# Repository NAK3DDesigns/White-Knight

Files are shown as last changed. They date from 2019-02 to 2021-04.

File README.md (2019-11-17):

# White-Knight
White Knight Belt Printer
This repository contains all files necessary to build you own White Knight Belt printer..
Please bear with me as I continue to update files and process assembly videos

I believe all files have been converted to Fusion 360 now.  If you discover a file I've missed please open a new issue and I will get it converted and uploaded.. 

There are people trying to organize group buys for the belt materials..  see link below..
https://infinityprinters.org/t/group-buy-endless-belt/67

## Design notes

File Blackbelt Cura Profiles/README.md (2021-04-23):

# Blackbelt Cura Profiles

****this is still in testing****
Please leave feedback

To use this executable file you first need to install Blackbelt Cura 3.6.0 and the 3.6.0 Update 1...
https://blackbelt-3d.com/download-area/
Once installed just run this executable, it will install new profiles in Cura.
Once in Cura go to "Preferences", "Configure Cura", select "Printers" in the left window,
click "Add", select "NAK 3D Designs" 
Choose "Squire" or " White Knight"

****Update****

This should still work with the latest 3.6.2 version.

There are other options now available as well that support belt printing.

IdeaMaker - https://www.raise3d.com/download/

Kiri:moto - https://grid.space/kiri/

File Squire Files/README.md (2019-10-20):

# White-Knight
White Knight Belt Printer
This repository contains all files necessary to build you own White Knight Squire Belt printer..
I will continue to add files and BOM as I get them completed.  Currently all Fusion 360 files, STEP files, & the STL's for the main printer have been loaded..
I have also added the Assembly files..  They are not complete with all minor hardware but all major components are in place..

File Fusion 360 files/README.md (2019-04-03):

# White-Knight
White Knight Belt Printer
This repository contains Fusion 360 Files that have been test printed and verified to have correct dimensions and fit.

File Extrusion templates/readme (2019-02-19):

Files for aluminum extrusion templaes and aluminum tool plates

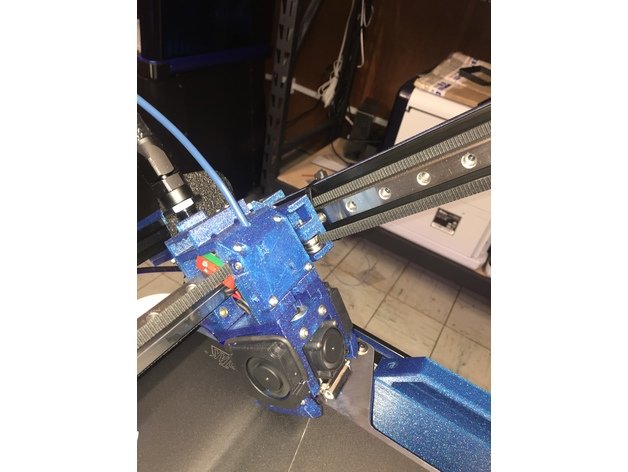
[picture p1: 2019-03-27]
Photos/White Knight 7.jpg

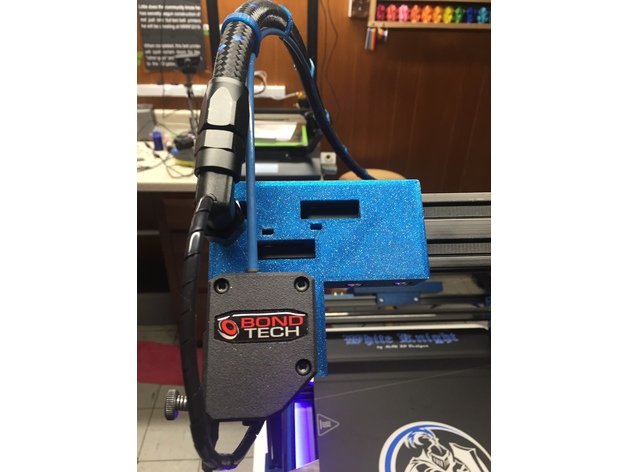
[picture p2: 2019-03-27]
Photos/White Knight 14.jpg

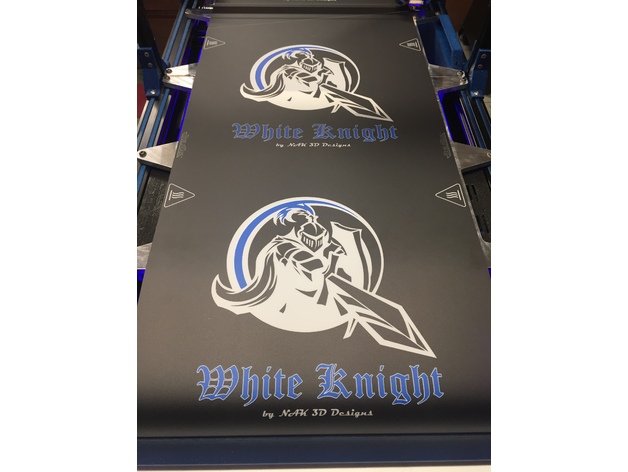
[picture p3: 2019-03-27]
Photos/White Knight 15.jpg

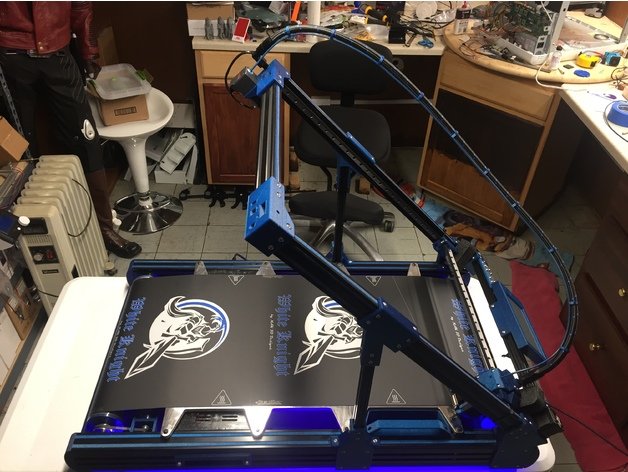
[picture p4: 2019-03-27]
Photos/White Knight 3.jpg

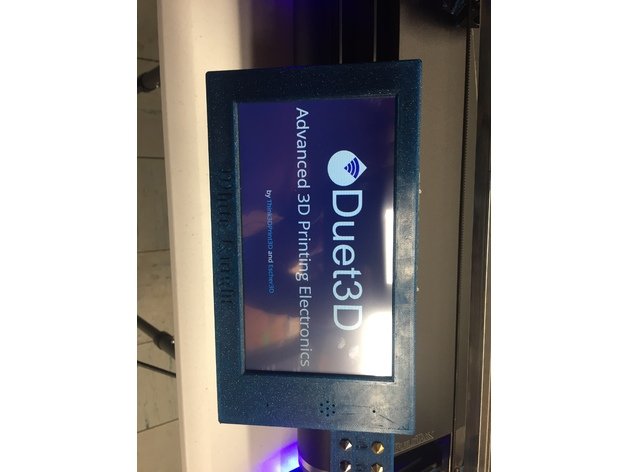
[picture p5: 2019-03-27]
Photos/White Knight 16.jpg

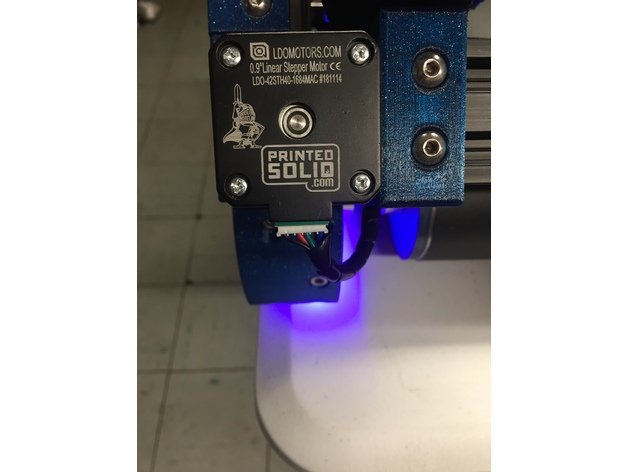
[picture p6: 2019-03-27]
Photos/White Knight 8.jpg

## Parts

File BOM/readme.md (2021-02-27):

# BOM
## Components
| Part | Qty | Cost | Source |
|---|-----|---|---|
| 100x Spring Loaded T-Nuts 2020 M4/M5 | 2 | $25.90  | Zyltec |
| MGN12 Linear Rail - 1000mm - One Carriage | 2 | $103.90 | Zyltec |
| MGN12 Linear Rail - 500mm - One Carriage | 1 | $34.95  | Zyltec |
| Extrusions | 1 | $154.39 | Openbuilds |
| Duet Wifi | 1 | $169.90 | Printed Solid |
| PanelDue 7i | 1 | $104.90 | Printed Solid |
| Bondtech BMG | 1 | $80.00  | Printed Solid |
| Mosquito Mount | 1 | $11.99  | Printed Solid |
| Mosquito Hotend | 1 | $144.80 | Printed Solid |
| Slice Thermistor | 1 | $39.99  | Printed Solid |
| Slice 50W heater | 1 | $18.80  | Printed Solid |
| LDO .9 Stepper | 3 | $45.00  | Printed Solid |
| Nema 17 5:1 geared stepper | 1 | $39.87  | E3D Online |
| F623zz Bearings | 20  | $12.00  | e-bay |
| 2GT Timing pulley 20Tooth 5mm Bore | 2 | $2.00 | e-bay |
| 2GT Timing pulley 20tooth 8mm Bore | 1 | $2.00 | e-bay |
| 60T 1/2 GT2 pulley | 1 | $13.00  | e-bay |
| 6202-2RS 1/2 ID bearing | 4 | $11.00  | thebigbearingstore.com |
| Micro switch endstop | 2 | $2.00 | Openbuilds |
| Aluminum tube 3"x16"x.125" (61ARDT3125) | 2 | $24.68  | Midweststeelsupply.com |
| Aluminum Tool Plate 3/8" x 15" x 20.5" (ALI38) | 1 | $50.64  | Midweststeelsupply.com |
| Aluminum tool plate 3/8" x 9" x 20.5" (ALI38) | 1 | $34.32  | Midweststeelsupply.com |
| 6061 Aluminum Square Bar 1/2" x 19" (61ASB12) | 1 | $7.95 | Midweststeelsupply.com |
| 303 Stainless Bearing Shaft(303SSBSQ12) 1/2 x 20.5"| 2 | $16.00  | Midweststeelsupply.com |
| Full hardened Stainless steel belt 400mm x 1920mm  | 1 | $265-$370 | Belttechnologies.com |
| **** Belt cost varies depending on Quantity ordered, group buys recommended  **** |
| Buildtak sheet 405mm x 2000mm (3 week lead time) | 1 | $290.00 | Buildtak.com |
| Meanwell LRS350-24 powersupply | 1 | $30.00  | Jameco.com #2219823 |
| Silicone Bed heater 200x400 24v(ebay item #143206149832)| 1 | $55.00  | e-bay |
| Rubber feet | 1 | $10.00  | e-bay |
| 1/2" x 19" aluminum sqaure bar | 1 | $7.95 | Midweststeelsupply.com |
| Noctua 40mm fans | 3 | $45.00  | Amazon |
| Roller drive belt A6R51M125060 | 1 | $6.00 | SDP/SI |
| 5 meters of GT2 Belt | 1 | $50.00  | SDP/SI |
| 24v Blower Fans | 2 | $18.00  | Tinymachines.com |
| stepper heat sink | 1 | $5.00 | Amazon part #A-0047 |
| Power Connector/switch | 1 | $3.00 | ebay item#152765834186 |
| Bulk Harware order (nuts, bolt, etc) | 1 | $202.73 | McMaster Carr |
| 3/8-in Push Connect x 1/4-in MIP Male Fitting | 1 | $3.78 | Lowes.com #835028 |
| 3/8-in Push Connect x 1/4-in MIP dia 90-Degree 	 | 1 | $4.18	 | Lowes.com #835045 |
| 3/8-in x 25-ft Polyethylene Tubing | 1 | $6.18 | Lowes.com #814305 |
|Buck converter (part # MP1584EN) | 1	 | $8.00	 | Amazon.com |

## Extrusions
| Size | Length | Qty |
|---|---|-----|
| 4080 C-Channel | 914mm  | 2 |
| 2040 V-slot | 520mm  | 3 |
| 2040 V-slot | 700mm  | 2 |
| 2040 V-slot | 460mm  | 1 |
| 2040 V-slot | 453mm  | 1 |
| 2020 V-slot | 315mm  | 2 |

## Bulk Hardware
| Item | Qty | Source | Part # | 
|---|-----|---|---|
| M2 x 12mm bolt | 8 | McMaster-Carr | 92095A455 | 
| M2 Nut | 2 | McMaster-Carr | 91828A111 | 
| M2 Heatset | 6 | McMaster-Carr | 94459A120 | 
| M3 Heatset | 48  | McMaster-Carr | 94180A331 | 
| M3 Washer | 18  | McMaster-Carr | 93475A210 | 
| M3 Star washer | 4 | McMaster-Carr | 95060A320 | 
| M3 Nut | 6 | McMaster-Carr | 91828A211 | 
| M3 x 8mm bolt | 46  | McMaster-Carr | 92095A181 | 
| M3 x 10mm bolt | 14  | McMaster-Carr | 92095A182 | 
| M3 x 12mm bolt | 10  | McMaster-Carr | 92095A183 | 
| M3 x 16mm bolt | 28  | McMaster-Carr | 92095A184 | 
| M3 x 18mm bolt | 2 | McMaster-Carr | 92095A472 | 
| M3 x 25mm bolt | 14  | McMaster-Carr | 92095A186 | 
| M3 x 30mm bolt | 1 | McMaster-Carr | 92095A187 | 
| M3 x 35mm bolt | 4 | McMaster-Carr | 92095A201 | 
| M3 x 45mm bolt | 2 | McMaster-Carr | 92095A474 | 
| M4 x 8mm bolt | 4 | McMaster-Carr | 92095A189 | 
| M5 Square nut | 4 | McMaster-Carr | 90225A101 | 
| M5 T-nuts | 118 | Zyltec.com | HW-M5-SPRNG-T-NUT-100PK | 
| M5 high temp washers | 10  | McMaster-Carr | 93785A214 | 
| M5 x 15mm high temp/nylon washer| 10  | | | 
| M5 x 8mm Button Bolt | 104 | McMaster-Carr | 92095A207 | 
| M5 x 16mm Bolt | 23  | McMaster-Carr | 91292A126 | 
| M5 x 18mm Button Bolt | 10  | McMaster-Carr | 92095A481 | 
| M5 x 30mm Bolt | 18  | McMaster-Carr | 91292A192 | 
| #2 x3/8in thread cutting screws | 2 | | | 
| JST connectors | 6 | ebay | | 
| Shaft Collar | 7 | McMaster-Carr | 9946K15 | 
| M3 x8mm Knurled screw | 2 | McMaster-Carr | 92545A111 | 

## Wire Harness
| Item | Qty | Source | Part # | 
|---|-----|---|---|
| 34 Pin Male IDC connector | 1 | TME.com | AWHP-34P | 
| 34 Pin Female IDC Connector | 1 | Digikey.com | 3M157228-ND | 
| 4 position Molex Plug | 1 | Digikey.com | WM1018-ND | 
| 4 position Molex receptical | 1 | Digikey.com | WM3701-ND | 
| Molex Male pin | 4 | Digikey.com | WM2500-ND | 
| Molex female pin | 4 | Digikey.com | WM2501-ND | 
| 20AWG 2 conductor blk/red | 1 | Digikey.com | CN180BR-25-ND | 
| 26AWG 34 cond multi color ribbon| 1 | Digikey.com | 3M157870-25-ND | 

## 34 pin connector pinout
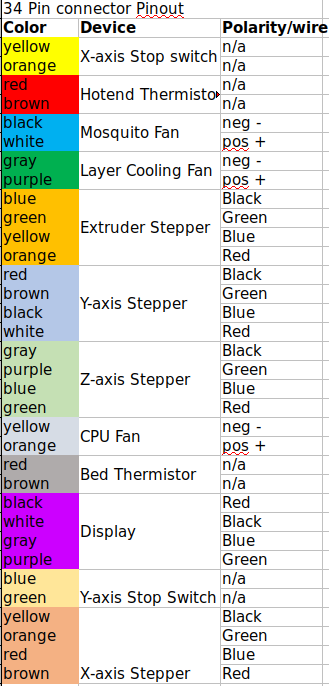
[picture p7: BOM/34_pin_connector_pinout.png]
pinout


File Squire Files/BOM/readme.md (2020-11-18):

# BOM
## Components
| Part | Qty | Cost | Source |
|---|-----|---|---|
| 100x Spring Loaded T-Nuts 2020 M4/M5 | 2 | $25.90  | Zyltec |
| LDO MGN12H Linear Rail - 400mm - Single Carriage | 3 | $120.00 | Printed Solid |
| Extrusions | 1 | $115.00 | Openbuilds |
| Duet Wifi | 1 | $169.90 | Printed Solid |
| Duet Filament Monitor Rotating Magnet Version | 1 | $52.95  | Printed Solid |
| PanelDue 5i | 1 | $89.90  | Printed Solid |
| Bondtech BMG | 1 | $80.00  | Printed Solid |
| E3Dv6 hotend & nozzle (hand filed edge) | 1 | $85.00  | Printed Solid |
| LDO .9 Stepper LDO-42STH40-1684MAC | 2 | $32.00  | Printed Solid |
| LDO .9 slim stepper LDO-42STH25-1404MAC | 1 | $15.00  | Printed Solid |
| LDO 5:1 geared stepper | 1 | $39.87  | Printed Solid |
| LDO 2GT 16T Idler with 3mm Bore | 8 | $48.00  | Printed Solid |
| Balitensen Toothless GT2 Idler Pulley 16T 3mm Bore | 2 | $7.90 | Amazon |
| 2GT Timing pulley 20Tooth 5mm Bore | 2 | $2.00 | e-bay |
| 2GT Timing pulley 20tooth 8mm Bore | 1 | $2.00 | e-bay |
| 6202-2RS 1/2 ID bearing | 3 | $9.00 | thebigbearingstore.com |
| Micro switch endstop | 2 | $2.00 | Openbuilds |
| Aluminum tube 3" x 9.5"x.125" (61ARDT3125) | 2 | $16.77  | Midweststeelsupply.com |
| Aluminum Tool Plate 1/4" x 4" x 15.75" (ALI38) | 1 | $16.39  | Midweststeelsupply.com |
| Aluminum tool plate 1/4" x 6" x 15.75" (ALI38) | 1 | $24.82  | Midweststeelsupply.com |
| 6061 Aluminum Square Bar 1/2" x 14.25" (61ASB12) | 1 | $7.95 | Midweststeelsupply.com |
| 303 Stainless Bearing Shaft 1/2" x 15.75"(303SSBSQ12)| 2 | $14.00  | Midweststeelsupply.com |
| Full hardened Stainless steel belt 240mm x 1085mm  | 1 | $265-370 | Belttechnologies.com  |
| **** Belt cost varies depending on Quantity ordered, group buys recommended  **** |
| Buildtak sheet 250mm x 1185mm (3 week lead time) | 1 | $175.00 | Buildtak.com |
| Meanwell LRS350-24 powersupply | 1 | $30.00  | Jameco.com #2219823 |
| Silicone Bed heater (ebay item #143351332434) | 1 | $34.00  | e-bay |
| SUNON 40mm fans | 5 | $52.00  | Printed Solid |
| Buck converter (part # MP1584EN)				 	 | 1 | $8.00 | Amazon.com |
| 8mm to 12mm shaft coupler | 1 | $10.25  | E-bay |
| 4 meters of GT2 Belt | 1 | $40.00  | Printed Solid |
| BerdAir  Max 24V with eswitch kit | 1 | $48.50  | themakerhive.com |
| stepper heat sink | 1 | $5.00 | Amazon part #A-0047 |
| Power Connector/switch | 1 | $3.00 | ebay item#152765834186 |
| Bulk Harware order (nuts, bolt, etc) | 1 | $202.73 | McMaster Carr |
| 3/8-in Push Connect x 1/4-in NPT Male Fitting | 2 | $15.06  | McMaster-Carr #5523K19 |
| 3/8-in x 25-ft Polyethylene Tubing | 1 | $6.18 | Lowes.com #814305 |

## Extrusions
| Size | Length | Qty |
|---|---|-----|
| 4080 C-Channel | 500mm  | 2 |
| 2040 V-slot | 400mm  | 4 |
| 2040 V-slot | 336mm  | 1 |
| 2040 V-slot | 370mm  | 1 |
| 2040 V-slot | 160mm  | 2 |
| 2040 V-slot | 387mm  | 2 |
| 2020 V-slot | 190mm  | 2 |

## Bulk Hardware
| Item | Qty | Source | Part # | 
|---|-----|---|---|
| M2.5 x 12mm bolt | 2 | McMaster-Carr | 92095A461 | 
| M2.5 Nut | 2 | McMaster-Carr | 91828A113 |
| M3 Heatset | 55  | McMaster-Carr | 94180A331 | 
| M3 Washer | 4 | McMaster-Carr | 93475A210 | 
| M3 Nut | 6 | McMaster-Carr | 91828A211 | 
| M3 x 8mm bolt | 60  | McMaster-Carr | 92095A181 | 
| M3 x 10mm bolt | 14  | McMaster-Carr | 92095A182 | 
| M3 x 12mm bolt | 10  | McMaster-Carr | 92095A183 | 
| M3 x 16mm bolt | 28  | McMaster-Carr | 92095A184 | 
| M3 x 18mm bolt | 2 | McMaster-Carr | 92095A472 | 
| M3 x 25mm bolt | 14  | McMaster-Carr | 92095A186 | 
| M3 x 30mm bolt | 1 | McMaster-Carr | 92095A187 | 
| M3 x 35mm bolt | 4 | McMaster-Carr | 92095A201 |
| M3 x 40mm bolt | 3 | McMaster-Carr | 92095A203 |
| M3 x 45mm bolt | 2 | McMaster-Carr | 92095A474 | 
| M4 x 8mm bolt | 8 | McMaster-Carr | 92095A189 | 
| M5 Square nut | 4 | McMaster-Carr | 90225A101 | 
| M5 T-nuts | 164 | Zyltec.com | HW-M5-SPRNG-T-NUT-100PK | 
| M5 high temp washers | 8 | McMaster-Carr | 93785A214 | 
| M5 x 15mm high temp/nylon washer| 8 | | | 
| M5 x 8mm Button Bolt | 156 | McMaster-Carr | 92095A207 | 
| M5 x 16mm Bolt | 21  | McMaster-Carr | 91292A126 | 
| M5 x 18mm Button Bolt | 8 | McMaster-Carr | 92095A481 | 
| M5 x 30mm Bolt | 12  | McMaster-Carr | 91292A192 | 
| #2 x3/8in thread cutting screws | 2 | | | 
| JST connectors | 6 | ebay | | 
| Shaft Collar | 6 | McMaster-Carr | 9946K15 |
| Stacked wave spring 5mm shaft | 4 | McMaster-Carr | 1561T732 | 

## Wire Harness
| Item | Qty | Source | Part # | 
|---|-----|---|---|
| 40 Pin Male IDC connector | 1 | Digikey.com | OR973-ND | 
| 40 Pin Female IDC Connector | 1 | Digikey.com | OR923-ND | 
| 4 position Molex Plug | 2 | Digikey.com | WM1018-ND | 
| 4 position Molex receptical | 2 | Digikey.com | WM3701-ND | 
| Molex Male pin | 4 | Digikey.com | WM2500-ND | 
| Molex female pin | 4 | Digikey.com | WM2501-ND | 
| 20AWG 2 conductor blk/red | 1 | Digikey.com | CN180BR-25-ND | 
| 26AWG 40 cond multi color ribbon| 1 | Digikey.com | 3M157900-25-ND | 

## Hotend Quick disconnect Bread Board
| Item | QTY | Source | Part # |
|---|-----|---|---|
| Molex MicroFit 3.0 6 Pos Header | 1 | Digikey.com | WM4037-ND |
| Molex Microfit 3.0 2 Pos header | 3 | Digikey.com | WM1922-ND |
| Molex Microfit 3.0 6 Pos Recpt  | 1 | Digikey.com | WM1785-ND |
| Molex Microfit 3.0 conn socket  | 25  | Digikey.com | WM1125CT-ND |
| Adafruit Jumper wire 22awg | 1 | Digikey.com | 1528-1743-ND |
| Gikfun Breadboard GK1009 | 1 | Amazon.com | GK1009 |

## 40 pin connector pinout
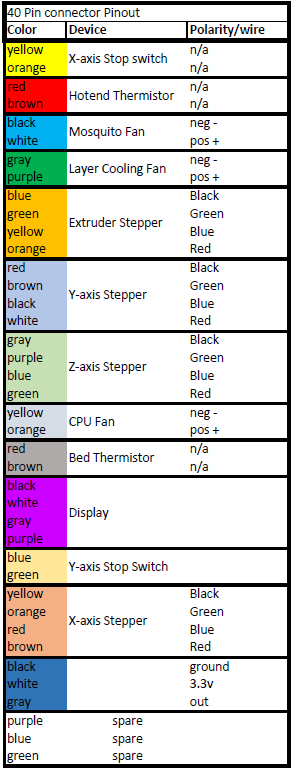
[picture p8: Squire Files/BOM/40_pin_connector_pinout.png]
pinout


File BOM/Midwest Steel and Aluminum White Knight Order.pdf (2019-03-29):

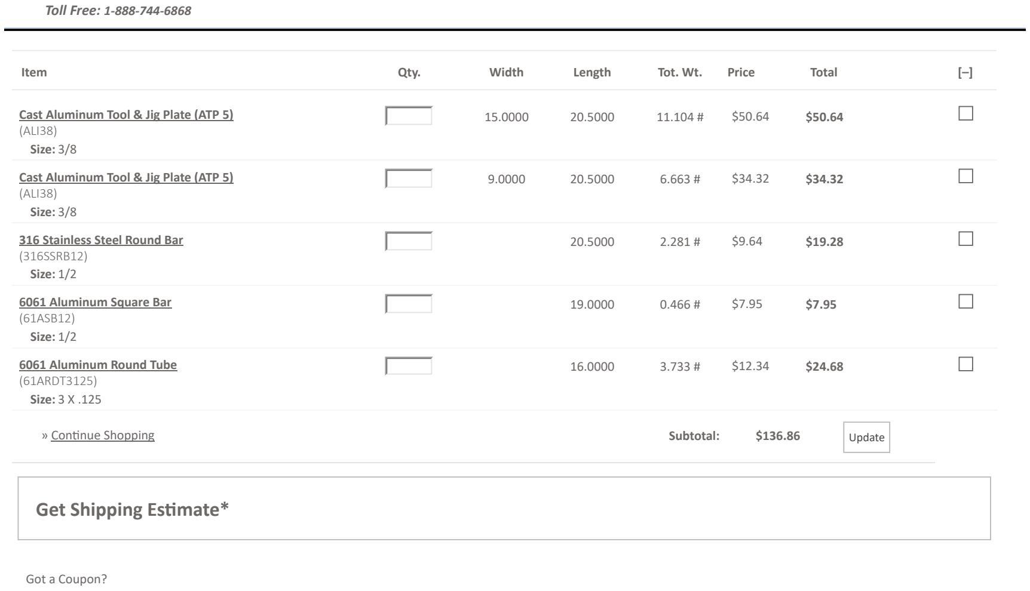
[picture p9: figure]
Toll Free: 1-888-744-6868; Cast Aluminum Tool & Jig Plate (ATP 5) (ALI38) Size: 3/8; 316 Stainless Steel Round Bar (316SSRB12) Size: 1/2; 6061 Aluminum Square Bar (61ASB12) Size: 1/2; 6061 Aluminum Round Tube (61ARDT3125) Size: 3 X .125; Item; Qty.; Width; Length; Tot. Wt.; Price; Total; » Continue Shopping; Subtotal:; Update; Get Shipping Estimate*; Got a Coupon?

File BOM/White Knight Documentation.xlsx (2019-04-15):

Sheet: 34pin connector
34 Pin connector Pinout
Color | Device | Polarity/wire
yellow | X-axis Stop switch | n/a
orange |  | n/a
red | Hotend Thermistor | n/a
brown |  | n/a
black | Mosquito Fan | neg -
white |  | pos +
gray | Layer Cooling Fan | neg -
purple |  | pos +
blue | Extruder Stepper | Black
green |  | Green
yellow |  | Blue
orange |  | Red
red | Y-axis Stepper | Black
brown |  | Green
black |  | Blue
white |  | Red
gray | Z-axis Stepper | Black
purple |  | Green
blue |  | Blue
green |  | Red
yellow | CPU Fan | neg -
orange |  | pos +
red | Bed Thermistor | n/a
brown |  | n/a
black | Display | Red
white |  | Black
gray |  | Blue
purple |  | Green
blue | Y-axis Stop Switch | n/a
green |  | n/a
yellow | X-axis Stepper | Black
orange |  | Green
red |  | Blue
brown |  | Red

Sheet: BOM
BOM |  |  |  | Total | $2042.92
Part | Cost | source
Linear Rails | $175.00 | Zyltec
Extrusions | $154.39 | Openbuilds
Duet Wifi | $169.90 | Printed Solid
PanelDue 7i | $104.90 | Printed Solid
Bondtech BMG | $80.00 | Printed Solid
Mosquito Mount | $11.99 | Printed Solid
Mosquito Hotend | $144.80 | Printed Solid
Slice Thermistor | $39.99 | Printed Solid
Slice 50W heater | $18.80 | Printed Solid
LDO .9 Stepper 1 | $15.00 | Printed Solid
LDO .9 Stepper 2 | $15.00 | Printed Solid
LDO .9 Stepper 3 | $15.00 | Printed Solid
Nema 17 5:1 geared stepper | $39.87 | E3D Online
623zz Bearings QTY 20 | $12.00 | e-bay
2GT Timing Pulley 20 Tooth 5mm bore | $2.00 | e-bay
2GT Timing Pulley 20 Tooth 8mm bore | $2.00 | e-bay
60T 1/2 GT2 pulley | $13.00 | e-bay
6202RS2 1/2 ID bearing QTY 4 | $11.00 | thebigbearingstore.com
Micro switch endstop Qty 2 | $2.00 | Openbuilds
Aluminum tube 3"x16"x.125" qty 2 | $24.68 | Midweststeelsupply.com
Aluminum Tool Plate 3/8" x 15" x 20.5" | $50.64 | Midweststeelsupply.com
Aluminum tool plate 3/8" x 9" x 20.5" | $34.32 | Midweststeelsupply.com
Stainless Steel Round Bar 1/2" x 20.5" | $19.28 | Midweststeelsupply.com
Full hardened Stainless steel belt 400mm x 1920mm | $210.00 | Belttechnologies.com
Buildtak sheet | $290.00 | Buildtak
Zyltec 2020 T-nuts Qty 200 | $30.00 | Zyltec
Meanwell LRS350-24 powersupply | $30.00 | jameco.com #2219823
Silicone Bed heater | $55.00 | e-bay
Rubber feet | $10.00 | e-bay
1/2" x 19" aluminum sqaure bar | $7.95 | Midweststeelsupply.com
Noctua 40mm fans Qty 3 | $45.00 | Amazon
3/8 PTFE, and fittings | $12.00 | Lowes
Roller drive belt A6R51M125060 | $6.00 | SDP/SI
5 meters of GT2 Belt | $50.00 | SDP/SI
24v Blower Fans QTY 2 | $18.00 | Tinymachines.com
stepper heat sink | $5.00 | ebay
Bulk Harware order (nuts, bolt, etc) | $202.73 | McMaster Carr | Broke down in Bulk hardware tab
34 Pin Male IDC connector | $1.32 | TME.com | AWHP-34P
34 Pin Female IDC Connector | $1.38 | Digikey.com | 3M157228-ND
4 position Molex Plug | $0.36 | Digikey.com | WM1018-ND
4 position Molex receptical | $0.31 | Digikey.com | WM3701-ND
Molex Male pin | $1.68 | Digikey.com | WM2500-ND
Molex female pin | $1.70 | Digikey.com | WM2501-ND
20AWG 2 conductor blk/red | $19.54 | Digikey.com | CN180BR-25-ND
26AWG 34 cond multi color ribbon | $50.25 | Digikey.com | 3M157870-25-ND
3/8-in Push Connect x 1/4-in MIP Male Fitting | $3.78 | Lowes.com #835028
3/8-in Push Connect x 1/4-in MIP dia 90-Degree | $4.18 | lowes.com #835045
3/8-in x 25-ft Polyethylene Tubing | $6.18 | lowes.com #814305

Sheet: Infill percentges
File | Infill | Nozzle | Perimeters | Layer Height
1-All_Belt_Clamps V2.stl | 85% | 0.4 | 4 | 0.2
1-Belt stepper mount Pt1 V4.stl | 50% | 0.4 | 4 | 0.2
1-Belt_stepper_mount_Pt2_V3.stl | 50% | 0.4 | 4 | 0.2
1-CBA bottom Cover V3 - part 1of3.stl | 5% | 0.8 | 2 | 0.2
1-CBA bottom Cover V3 - part 2of3.stl | 5% | 0.8 | 2 | 0.2
1-CBA bottom Cover V3 - part 3of3.stl | 5% | 0.8 | 2 | 0.2
1-CBA bottom Cover V3 Full.stl | 5% | 0.8 | 2 | 0.2
1-CBA top Cover V5 part 1of3.stl | 5% | 0.8 | 2 | 0.2
1-CBA top Cover V5 part 2of3.stl | 5% | 0.8 | 2 | 0.2
1-CBA top Cover V5 part 3of3.stl | 5% | 0.8 | 2 | 0.2
1-CBA top Cover V5.stl | 5% | 0.8 | 2 | 0.2
1-CBA_slide_tray_assembly_v11.stl | 25% | 0.4 | 4 | 0.2
1-Cooling fan Ducts v4.stl | 50% | 0.4 | 4 | 0.2
1-Display_Support_Endcaps.stl | 25% | 0.4 | 4 | 0.2
1-Mosquito & E3Dv6 Mount V7.stl | 50% | 0.4 | 4 | 0.2
1-Mosquito & E3Dv6 clamp and cooling fan mount V4.stl | 50% | 0.4 | 4 | 0.2
1-PanelDue7i_mount.stl | 50% | 0.4 | 4 | 0.2
1-PanelDue_7i_Version_2_Back.stl | 50% | 0.4 | 4 | 0.2
1-PanelDue_7i_Version_2_Front WK.stl | 50% | 0.4 | 4 | 0.2
1-Peeler.stl | 0% | 0.8 | 2 | 0.4
1-Rear_Idler_Right_V5.stl | 50% | 0.4 | 4 | 0.2
1-Rear_Idler_left_V4.stl | 50% | 0.4 | 4 | 0.2
1-Side_Support_Top_Brace_Left_V2.stl | 50% | 0.4 | 4 | 0.2
1-Side_Support_Top_Brace_Right_V2.stl | 50% | 0.4 | 4 | 0.2
1-Stepper_Mount_Left_V9.stl | 50% | 0.4 | 4 | 0.2
1-Stepper_Mount_Right_V9.stl | 50% | 0.4 | 4 | 0.2
1-Xaxis_Mount_Left_V11.stl | 50% | 0.4 | 4 | 0.2
1-Xaxis_Mount_Right_V10.stl | 50% | 0.4 | 4 | 0.2
1-hotend wire cover V3.stl | 50% | 0.4 | 4 | 0.2
1-hotend_carriage_v6.stl | 50% | 0.4 | 4 | 0.2
1-plug mount.stl | 50% | 0.4 | 4 | 0.2
1-slide tray end cover v4.stl | 50% | 0.4 | 4 | 0.2
1-tensioner mount bracket.stl | 50% | 0.4 | 4 | 0.2
10-Bowden_Cable_Clip_V1.stl | 85% | 0.4 | 4 | 0.2
2-4080 c-beam endcap V5.stl | 50% | 0.4 | 4 | 0.1
2-4080 c-beam endcap wider v1.stl | 50% | 0.4 | 4 | 0.1
2-Roller_Insert.stl | 25% | 0.4 | 4 | 0.2
2-Side_Support_Bottom_Brace.stl | 50% | 0.4 | 4 | 0.2
3-Pulley_Bearing_Mount_V2.stl | 50% | 0.4 | 4 | 0.2
4-Roller_End_Cap.stl | 25% | 0.4 | 4 | 0.2
switch enclosure V4.stl | 85% | 0.4 | 4 | 0.2
Drip Tray V2.stl | 50% | 0.4 | 4 | 0.2
Drip Tray handle.stl | 50% | 0.4 | 4 | 0.2

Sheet: Extrusions
Extrusions
Size | Length | Quantity
4080 C-Channel | 914mm | 2
2040 V-slot | 520mm | 3
2040 V-slot | 700mm | 2
2040 V-slot | 460mm | 1
2040 V-slot | 453mm | 1
2020 V-slot | 315mm | 2

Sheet: Bulk Hardware
Item | Qty | source | part#
M2 x 12mm bolt | 8 | McMaster-Carr | 92095A455
M2 Nut | 2 | McMaster-Carr | 91828A111
M2 Heatset | 6 | McMaster-Carr | 94459A120
M3 Heatset | 48 | McMaster-Carr | 94180A331
M3 Washer | 18 | McMaster-Carr | 93475A210
M3 Star washer | 4 | McMaster-Carr | 95060A320
M3 Nut | 6 | McMaster-Carr | 91828A211
M3 x 8mm bolt | 46 | McMaster-Carr | 92095A181
M3 x 10mm bolt | 14 | McMaster-Carr | 92095A182
M3 x 12mm bolt | 10 | McMaster-Carr | 92095A183
M3 x 16mm bolt | 28 | McMaster-Carr | 92095A184
M3 x 18mm bolt | 2 | McMaster-Carr | 92095A472
M3 x 25mm bolt | 14 | McMaster-Carr | 92095A186
M3 x 30mm bolt | 1 | McMaster-Carr | 92095A187
M3 x 35mm bolt | 4 | McMaster-Carr | 92095A201
M3 x 45mm bolt | 2 | McMaster-Carr | 92095A474
M4 x 8mm bolt | 4 | McMaster-Carr | 92095A189
M5 Square nut | 4 | McMaster-Carr | 90225A101
M5 T-nuts | 118 | Zyltec.com | HW-M5-SPRNG-T-NUT-100PK
M5 high temp washers | 10 | McMaster-Carr | 93785A214
M5 x 15mm custom washer | 10
M5 x 8mm Button Bolt | 104 | McMaster-Carr | 92095A207
M5 x 16mm Bolt | 23 | McMaster-Carr | 91292A126
M5 x 18mm Button Bolt | 10 | McMaster-Carr | 92095A481
M5 x 30mm Bolt | 18 | McMaster-Carr | 91292A192
#2 x3/8in thread cutting screws | 2
JST connectors | 6
Shaft Collar | 7 | McMaster-Carr | 9946K15
M3 x8mm Knurled screw | 2 | McMaster-Carr | 92545A111

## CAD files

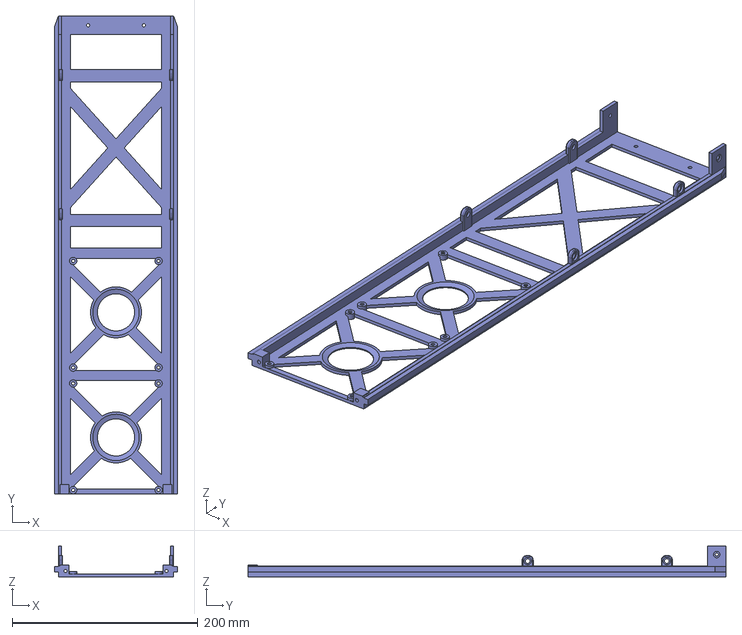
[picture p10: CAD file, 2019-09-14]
Fusion 360 files/1-CBA_slide_tray_assembly_v11 v2.step
133.1 x 515.2 x 33.0 mm

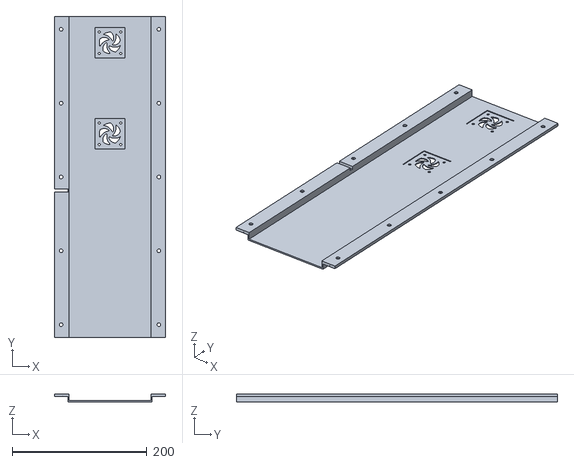
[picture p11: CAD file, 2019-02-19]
Printer STL's/1-CBA bottom Cover V3 Full.stl
165.0 x 476.0 x 12.0

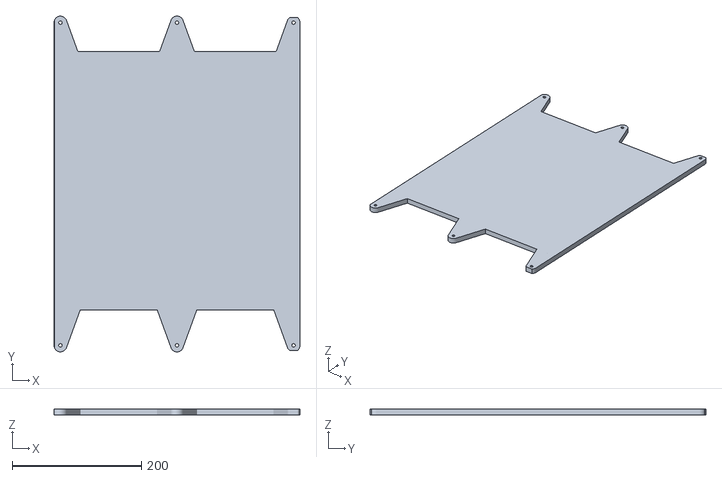
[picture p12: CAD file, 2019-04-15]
Extrusion templates/1x-Cold Build Plate V3.stl
381.0 x 520.0 x 9.52

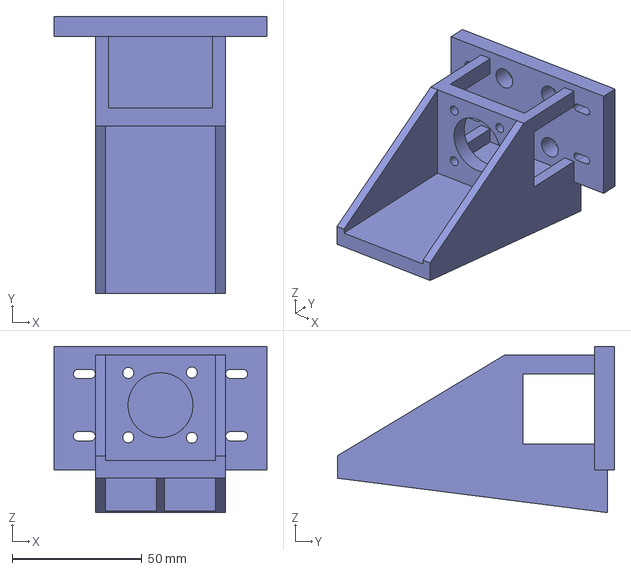
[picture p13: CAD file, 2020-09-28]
Fusion 360 files/1-Belt stepper mount Pt1 - LDO-42STH40-1204ACPG5 - V1.step
82.0 x 106.8 x 64.0 mm

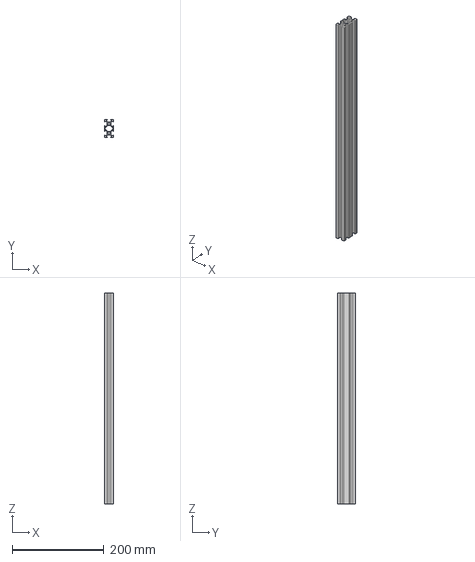
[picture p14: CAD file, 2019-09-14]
Fusion 360 files/Extrusion templates/1x 460mm 2040 v1.step
20.0 x 40.0 x 460.0 mm

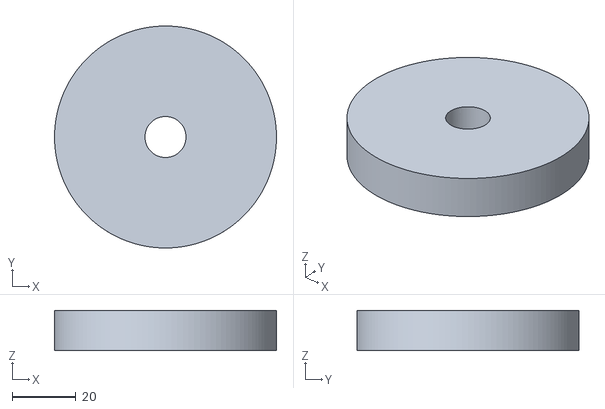
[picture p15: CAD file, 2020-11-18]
Printer STL's/2-Roller_Insert.stl
69.8 x 69.8 x 12.7

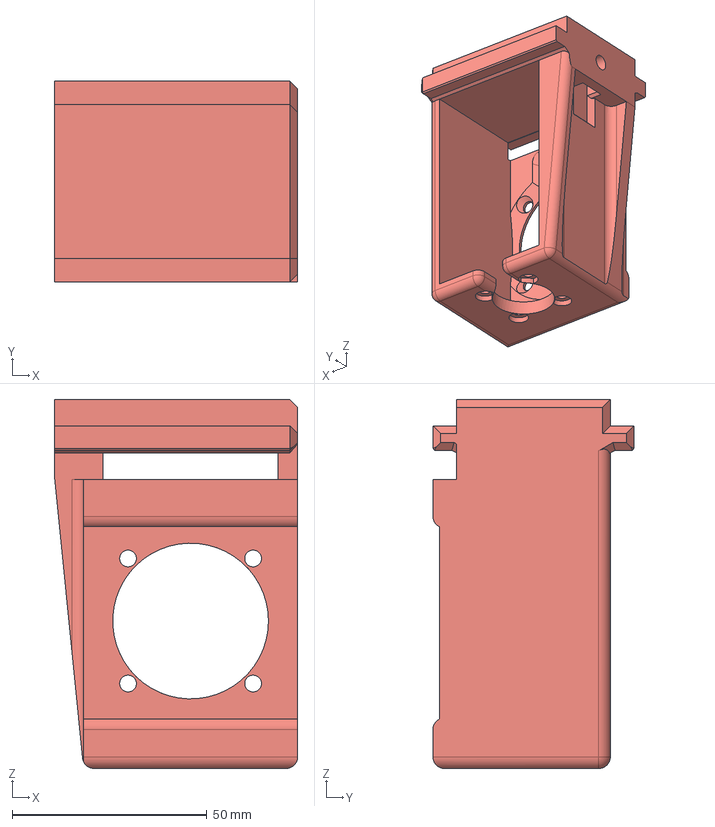
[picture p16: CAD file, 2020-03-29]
Squire Files/STEP Files/1-Belt Stepper direct drive Mount2 for E3D v2.step
62.5 x 51.7 x 94.8 mm

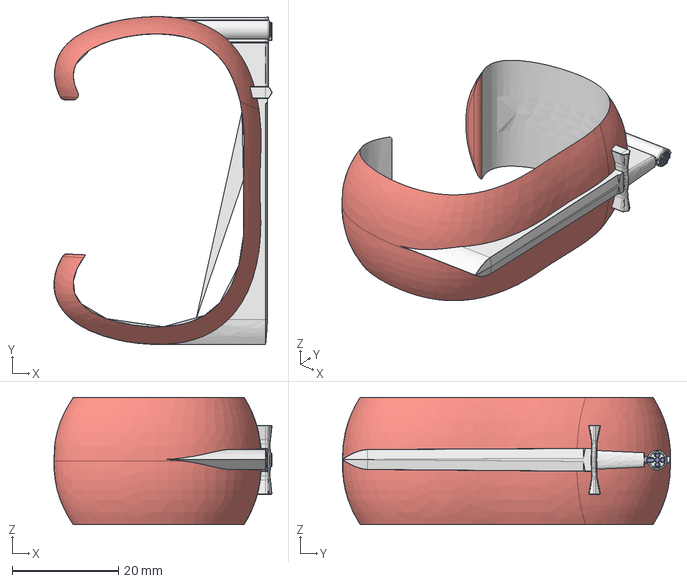
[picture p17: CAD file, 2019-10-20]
Squire Files/STEP Files/Scales/2040 extrusion top cover part 3.step
41.1 x 61.8 x 24.0 mm

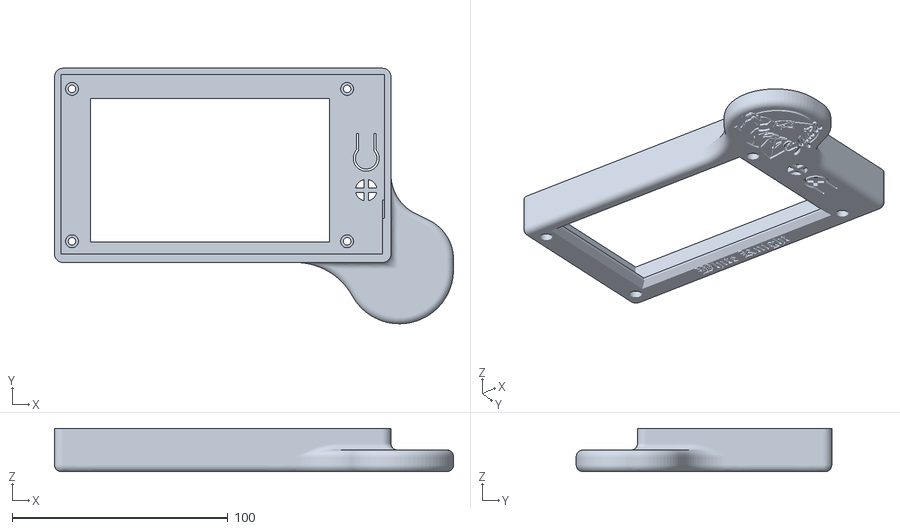
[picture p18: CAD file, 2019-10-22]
Squire Files/STL Files/1-5i_Case_Front Knight v14.stl
184.9 x 118.4 x 20.0

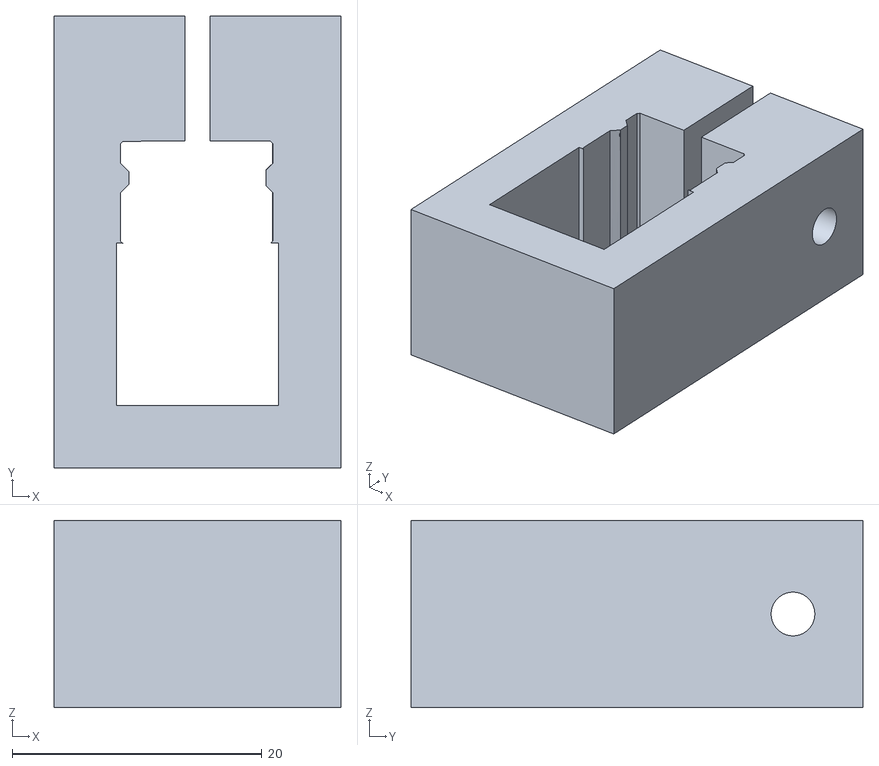
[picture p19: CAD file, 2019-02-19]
Tools STL's/linear rail alignment tool 2.stl
23.0 x 36.2 x 15.0

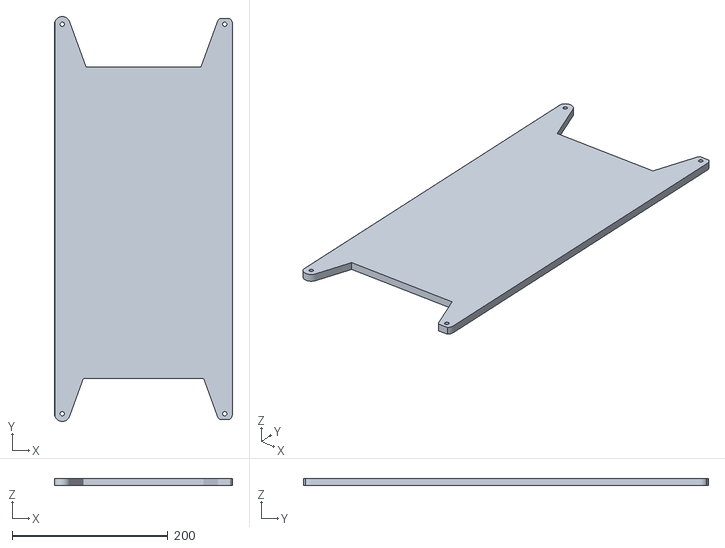
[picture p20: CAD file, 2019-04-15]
Extrusion templates/1x-Heated Build Plate V3.stl
228.6 x 520.0 x 9.53

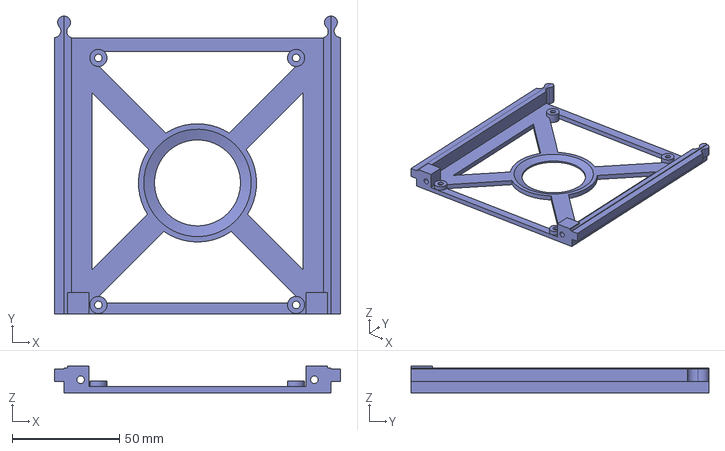
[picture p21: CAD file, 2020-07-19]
Fusion 360 files/CBA _Slide_Tray_Part_1of4 v2.step
133.1 x 138.7 x 12.5 mm

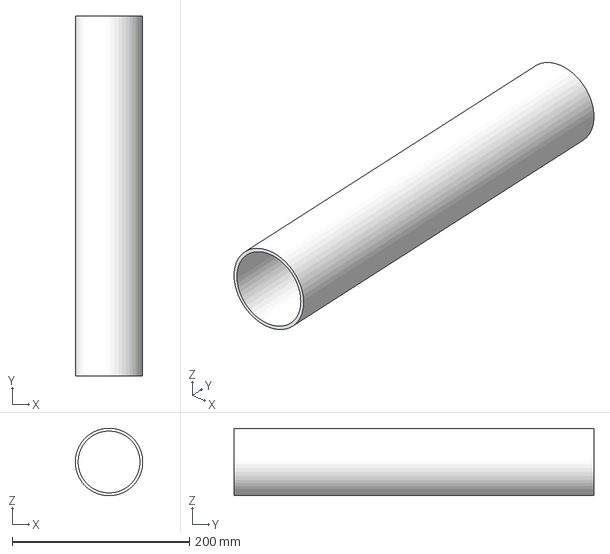
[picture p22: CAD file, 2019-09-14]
Fusion 360 files/Extrusion templates/2-3 inch aluminum roller tube v3.step
76.1 x 406.4 x 76.2 mm

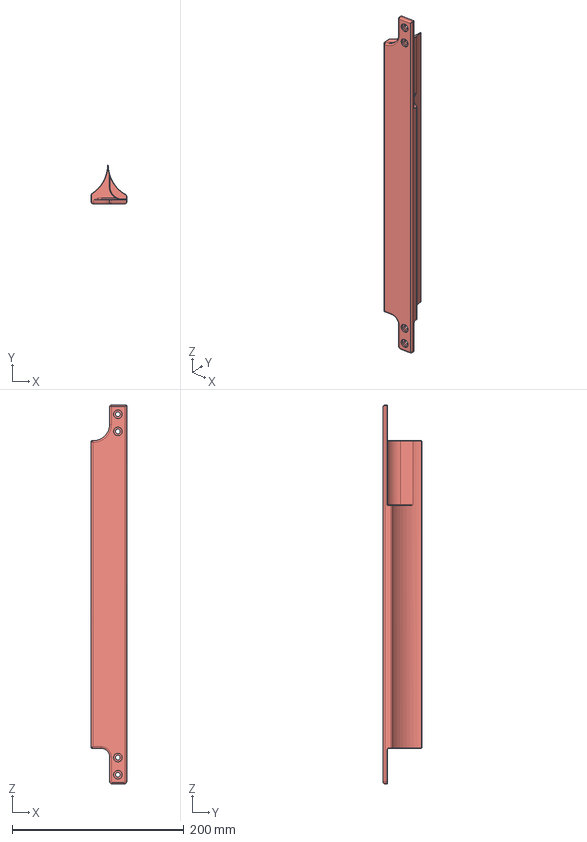
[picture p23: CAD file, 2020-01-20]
Squire Files/STEP Files/1-Peeler V4 v2.step
41.4 x 45.0 x 441.0 mm

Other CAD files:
Fusion 360 files/1-CBA_bottom_Cover_V3_Full v2.step
Printer STL's/1-Belt stepper mount Pt1 - LDO-42STH40-1204ACPG5 - V1.stl
Squire Files/STL Files/1-Squire CBA Top Cover 2 v2 part 1.stl
Tools STL's/roller jig.stl
Extrusion templates/1x-Cold Build Plate.stl
Extrusion templates/1x-Heated Build Plate.stl
Extrusion templates/1x_453mm_2040.stl
Extrusion templates/1x_460mm_2040.stl
Extrusion templates/2x_315mm_2020.stl
Extrusion templates/2x_700mm_2040.stl
Extrusion templates/3x_520mm_2040.stl
Fusion 360 files/1-Belt stepper mount Pt1 - LDO-42STH40-1204ACPG5 - V1.f3d
Fusion 360 files/1-Belt stepper mount Pt1 V4 v3.f3d
Fusion 360 files/1-Belt stepper mount Pt1 V4 v3.step
Fusion 360 files/1-Belt_Clamp_2 v3.f3d
Fusion 360 files/1-Belt_Clamp_2 v3.step
Fusion 360 files/1-Belt_Clamp_3 v4.f3d
Fusion 360 files/1-Belt_Clamp_3 v4.step
Fusion 360 files/1-Belt_stepper_mount_Pt2_V3 v2.f3d
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

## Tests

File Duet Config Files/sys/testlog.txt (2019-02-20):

2018-06-06 13:45:55 Event logging started
2018-06-06 13:46:18 Warning: VIN under-voltage event (4.6V)
2018-06-06 13:46:47 Event logging started
2018-06-06 13:47:03 HTTP client 192.168.1.85 login succeeded
2018-06-06 13:49:07 Warning: VIN under-voltage event (4.6V)

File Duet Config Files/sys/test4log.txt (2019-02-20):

2018-11-24 12:22:30 Event logging started
2018-11-24 12:22:39 Event logging stopped

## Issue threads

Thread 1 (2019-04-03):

Update BOM to use markdown files

ArmoredBlood, 2019-04-03:
the current BOM is awkward to read since it needs a spreadsheet application just to open. I suggest consolidating the BOM and the order pdf's into a single readme.md that contains all the info of all the original spreadsheet and pdf's.

servant74, 2019-04-03:
Try this, the link has a PDF you can check out.  I don't have update privleges.  This is a conversion using Google Docs.

[White Knight BOM.pdf](https://github.com/NAK3DDesigns/White-Knight/files/3036523/White.Knight.BOM.pdf)

ArmoredBlood, 2019-04-03:
If you check out #2 I added the connector as an image and it's embedded in the BOM readme.md file. This way you don't need to download anything just to view the contents, it can all be viewed directly in your browser

servant74, 2019-04-03:
Thanks

NAK3DDesigns, 2019-04-04:
This issue has been merged with master.  Closing issue... PR#2

Closed 2019-04-04.

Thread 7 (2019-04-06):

Claim STL files you want to convert to STEP / Fusion 360

3d-gussner, 2019-04-06:
Just an idee:
Wouldn't it make sense if people claim ONE STL file at the time they are converting to STEP / Fusion 360? Or making a conversion status list:

| STL | Part of STL | Who | Status | ETD |Info| Reviewed |
| --------------------------- | ------------------- | ---------- | ------ | ------- |--------|-------|
| _1-All_Belt_Clams V2.stl_ | clam nr. 1 | @3d-gussner | [Done](https://github.com/NAK3DDesigns/White-Knight/blob/Development/Fusion%20360%20files/1-Belt-clamp_1.f3d)  | 04 april 2019 ||||
| _1-All_Belt_Clams V2.stl_ | clam nr. 2 | @3d-gussner | [Done](https://github.com/NAK3DDesigns/White-Knight/blob/Development/Fusion%20360%20files/1-Belt-clamp_1.f3d)  | 04 april 2019 |same as part 1||
| _1-All_Belt_Clams V2.stl_ | clam nr. 3 | @NicoSchlueter | [Done](https://github.com/NAK3DDesigns/White-Knight/pull/20) | 09 april  2019|||
| _1-All_Belt_Clams V2.stl_ | clam nr. 4 | @NicoSchlueter | [Done](https://github.com/NAK3DDesigns/White-Knight/pull/20) | 09 april  2019|||
| _1-Belt stepper mount Pt1 V4.stl_ | Just one | @EXOgreen | [Done](https://github.com/NAK3DDesigns/White-Knight/blob/Development/Fusion%20360%20files/1-Belt%20stepper%20mount%20Pt1%20V4.f3d) | 05 april 2019|[Step added](https://github.com/NAK3DDesigns/White-Knight/pull/15)||
| _1-Belt_stepper_mount_Pt2_V3.stl_ | Just one | @EXOgreen | [Done](https://github.com/NAK3DDesigns/White-Knight/pull/15) | 10 april 2019 |||
| _1-CBA bottom Cover V3 - part 1of3.stl_| Just one | @dsk001 | [Done](https://github.com/NAK3DDesigns/White-Knight/blob/Development/Fusion%20360%20files/1-CBA%20bottom%20Cover%20V3%20-%20part%201of3%20v1.f3d) | 06 april 2019|||
| _1-CBA bottom Cover V3 - part 2of3.stl_| Just one | @dsk001 | [Done](https://github.com/NAK3DDesigns/White-Knight/blob/Development/Fusion%20360%20files/1-CBA%20bottom%20Cover%20V3%20-%20part%202of3%20v1.f3d) | 06 april 2019|||
| _1-CBA bottom Cover V3 - part 3of3.stl_| Just one | @dsk001 | [Done](https://github.com/NAK3DDesigns/White-Knight/blob/Development/Fusion%20360%20files/1-CBA%20bottom%20Cover%20V3%20-%20part%203of3%20v1.f3d) | 06 april 2019|||
| _1-CBA bottom Cover V3 Full.stl_| Just one | @NicoSchlueter | [Done](https://github.com/NAK3DDesigns/White-Knight/pull/24) | 09 april  2019|||
| _1-CBA top Cover V5 part 1of3.stl_| Just one | @NicoSchlueter | [Done](https://github.com/NAK3DDesigns/White-Knight/pull/16) | 09 april  2019|||
| _1-CBA top Cover V5 part 2of3.stl_| Just one | @NicoSchlueter | [Done](https://github.com/NAK3DDesigns/White-Knight/pull/22) | 09 april  2019|||
| _1-CBA top Cover V5 part 3of3.stl_| Just one | @NicoSchlueter | [Done](https://github.com/NAK3DDesigns/White-Knight/pull/22) | 09 april  2019|||
| 1-CBA top Cover V5.stl| Just one | @NicoSchlueter | [Done](https://github.com/NAK3DDesigns/White-Knight/pull/22) | 09 april  2019|||
| _1-CBA_slide_tray_assembly_v11.stl_ | Just one | @NicoSchlueter | [Done](https://github.com/NAK3DDesigns/White-Knight/pull/25) | 09 april  2019|||
| _1-Cooling fan Ducts v4.stl_ |left one | @EXOgreen | [Done](https://github.com/NAK3DDesigns/White-Knight/pull/15) | 09 apr 2019|||
| _1-Cooling fan Ducts v4.stl_ |right one | @EXOgreen | [Done](https://github.com/NAK3DDesigns/White-Knight/pull/15) | 09 apr 2019|||
| _1-Display_Support_Endcaps.stl_ | short one | @reFlex-lab @NicoSchlueter | [Done](https://github.com/NAK3DDesigns/White-Knight/pull/21) | 09 april  2019|||
| _1-Display_Support_Endcaps.stl_ | wide one | @reFlex-lab @NicoSchlueter | [Done](https://github.com/NAK3DDesigns/White-Knight/pull/21) | 09 april  2019|||
| _1-Mosquito & E3Dv6 Mount V7.stl_| Just one | @ianespana | [Done](https://github.com/NAK3DDesigns/White-Knight/pull/26) | 10 april 2019|||
| _1-Mosquito & E3Dv6 clamp and cooling fan mount V4.stl_| Just one | @ianespana | [Done](https://github.com/NAK3DDesigns/White-Knight/pull/34) | 10 april 2019|||
| _1-PanelDue7i_mount.stl_| Just one | @ianespana | [Done](https://github.com/NAK3DDesigns/White-Knight/pull/34) | 10 april 2019|||
| _1-Peeler.stl_| Just one_ | @3d-gussner | [Done](https://github.com/NAK3DDesigns/White-Knight/pull/27) | 10 april 2019 |||
| _1-Rear_Idler_Right_V5.stl_| Just one | @ianespana | [Done](https://github.com/NAK3DDesigns/White-Knight/pull/34) | 10 april 2019|||
| _1-Rear_Idler_left_V4.stl_| Just one | @ianespana | [Done](https://github.com/NAK3DDesigns/White-Knight/pull/34) | 10 april 2019|||
| _1-Side_Support_Top_Brace_Left_V2.stl_ | Just one | @3d-gussner | [Done](https://github.com/NAK3DDesigns/White-Knight/pull/32) | 10 april 2019 |||
| _1-Side_Support_Top_Brace_Right_V2.stl_ | Just one | @3d-gussner | [Done](https://github.com/NAK3DDesigns/White-Knight/pull/32) | 10 april 2019 |||
| _1-Stepper_Mount_Left_V9.stl_ | Just one | @NicoSchlueter | [Done](https://github.com/NAK3DDesigns/White-Knight/pull/33)| 10 april 2019|||
| _1-Stepper_Mount_Right_V9.stl_ | Just one | @NicoSchlueter | [Done](https://github.com/NAK3DDesigns/White-Knight/pull/35) | 10 april 2019|||
| _1-hotend wire cover V3.stl_ | Just one | @NicoSchlueter | [Done](https://github.com/NAK3DDesigns/White-Knight/pull/29) | 10 april 2019 |||
| _1-hotend_carriage_v6.stl_ | Just one | @NicoSchlueter | [Done](https://github.com/NAK3DDesigns/White-Knight/pull/30) | 10 april 2019 |||
| _1-plug mount.stl_ | large part | @paulbuzzby | [Done](https://github.com/NAK3DDesigns/White-Knight/pull/36) | 10 april 2019 |||
| _1-plug mount.stl_ | small part | @paulbuzzby | [Done](https://github.com/NAK3DDesigns/White-Knight/pull/36) | 10 april 2019|||
| _1-slide tray end cover v4.stl_ | Just one | @3d-gussner | [Done](https://github.com/NAK3DDesigns/White-Knight/pull/31) | 10 april 2019 |||
| _1-tensioner mount bracket.stl_ | Just one | @NicoSchlueter | [Done](https://github.com/NAK3DDesigns/White-Knight/pull/28) | 10 april 2019 |||
| _1-Xaxis_Mount_Left_V11.stl_ | Just one | @3d-gussner | [PR](https://github.com/NAK3DDesigns/White-Knight/pull/43) | 14 april 2019 |||
| _1-Xaxis_Mount_Right_V10.stl_ | Just one | @3d-gussner | [Done](https://github.com/NAK3DDesigns/White-Knight/pull/38) | 11 april 2019 |||
| _10-Bowden_Cable_Clip_V1.stl_ | Just one | @3d-gussner | [Done](https://github.com/NAK3DDesigns/White-Knight/pull/14) | 08 april 2019 ||@eddie-moser|
| _2-4080 c-beam endcap V5.stl_ | Just one | @NicoSchlueter | [Done](https://github.com/NAK3DDesigns/White-Knight/pull/23) | 10 april 2019 |||
| _2-4080 c-beam endcap wider v1.stl_ | Just one | @NicoSchlueter | [Done](https://github.com/NAK3DDesigns/White-Knight/pull/23) | 10 april 2019 |||
| _2-Roller_Insert v1_ | Just one | @eddie-moser | [Done](https://github.com/NAK3DDesigns/White-Knight/blob/Development/Fusion%20360%20files/2-Roller_Insert%20v1.f3d) | 06 april 2019 |||
| _2-Side_Support_Bottom_Brace.stl_ | Just one | @NicoSchlueter | [Done](https://github.com/NAK3DDesigns/White-Knight/pull/19) | 10 april 2019 |||
| _3-Pulley_Bearing_Mount_V2.stl_ | Just one | @NicoSchlueter | [Done](https://github.com/NAK3DDesigns/White-Knight/pull/18) | 10 april 2019 |||
| _4-Roller_End_Cap v2.stl_ | Just one | @eddie-moser | [Done](https://github.com/NAK3DDesigns/White-Knight/blob/Development/Fusion%20360%20files/4-Roller_End_Cap%20v2.f3d) | 06 april 2019 |||
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
ianespana, 2019-04-12:
I think we can begin dry fitting all pieces without the need to have all the models of the non printed parts.
That being said we do need them, as later on we need to check clearances and what not

3d-gussner, 2019-04-12:
@ianespana I agree ... Question is if @NAK3DDesigns wants to make the assembly himself. As in the interview with Walter from Kuntry 3d he "complained" (not really complained :-) ) that he had no chance to learn Fusion 360 and convert these parts himself as we have done it in few days.

I will start my own assembly and let's see what he says.

NAK3DDesigns, 2019-04-12:
@3d-gussner power switch has been added to the BOM.  TMC home detection? Never heard of it..(remember I'm actually relatively new to 3D printing)  Honestly just tried to keep the design as simple as possible.

NAK3DDesigns, 2019-04-12:
@everyone @ianespana Sorry I did not mean it to sound like i was complaining, just the opposite I can't believe how fast you guys are doing this..  My only problem is I'm struggling to keep up as I don't know github or fusion. lol..  Feel free to proceed with making an assembly..  If you want a new folder just let me know..

3d-gussner, 2019-04-12:
@NAK3DDesigns Don't be sorry, it wasn't real complain we know that. I created few pull requests with Electronics and Hardware folder.

Maybe you should try to do the assembly your self and we are doing the same but maybe we can agree not to post changes of 3d printed parts until you give us the feedback.

It would be great if everybody tries to fit/assembly the parts and if there is an issue/tolerances/clearances/etc open here on github a new issue report, so we can discuss one by one.

3d-gussner, 2019-04-12:
> @3d-gussner power switch has been added to the BOM. TMC home detection? Never heard of it..(remember I'm actually relatively new to 3D printing) Honestly just tried to keep the design as simple as possible.

The Trinamic stepper drivers on the DuetWiFi can do sensorless homing as they can detect if the stepper hit something or not. On the other side micro switches aren't that bad and maybe having these in the design makes it even more open hardware, as people can use other boards to run it. (Budget WhiteKnight)

ianespana, 2019-04-12:
> > @3d-gussner power switch has been added to the BOM. TMC home detection? Never heard of it..(remember I'm actually relatively new to 3D printing) Honestly just tried to keep the design as simple as possible.
>
> The Trinamic stepper drivers on the DuetWiFi can do sensorless homing as they can detect if the stepper hit something or not. On the other side micro switches aren't that bad and maybe having these in the design makes it even more open hardware, as people can use other boards to run it. (Budget WhiteKnight)

I'm now wondering how well would that work with the reduction from the steppers...
My guess is could end up damaging the printer

3d-gussner, 2019-04-12:
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

As the geared motor is on the belt and this one doesn't need a endstop, it is not an issue. The other two steppers to move the head it shouldn't be an issue

3d-gussner, 2019-04-14:
@NAK3DDesigns Sorry for the late 1-Xaxis_Mount_Left PR.

EXOgreen, 2019-04-14:
do we want a folder of all the mcmaster carr hardware step files? I can run through and download those

3d-gussner, 2019-04-14:
> do we want a folder of all the mcmaster carr hardware step files? I can run through and download those

I think it is a great idea, as we can upload all files to Fusion 360 and make than an assembly from these. Please just add some "readable" names to the part numbers :-)

EXOgreen, 2019-04-14:
Hardware | Link | STEP file
------------ | ------------- | -------------
M5 spring loaded T-nuts | http://www.zyltech.com/100x-zyltech-spring-loaded-t-nuts-for-2020-aluminum-extrusion-m4-or-m5/ | your name here!
JST connectors | Link? | probably very fun to model...
#2 x3/8in thread cutting screws | not 100% sure what these are or where they are used, but a #2 thread is in fusion so should be pretty simple to make/fake |  your name here!

user577, 2019-04-14:
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

The #2 screws are self tapping sheet metal screws for the lcd enclosure.

The jst connectors are molex jst series (super common) there should be a multitude of models of these floating around.

the m5 nut is listed on mcmaster carr here. https://www.mcmaster.com/=1hmmz4w

I am also a github newbie so im not really sure where to add this info other than to comment on your post.

EXOgreen, 2019-04-14:
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

Ill look more into the screw and JST connectors, thanks for the info! For the M5 nut, your link seems to be broken, and as far as I can see McMaster doesn't have,
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

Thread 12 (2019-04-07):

Possible infringement of Stratasys patents

milkey-mouse, 2019-04-07:
I'm not a lawyer, but the main reason I didn't experiment with infinite-volume/belt-based 3D printers before was Stratasys patents [US8282380](https://patents.google.com/patent/US8282380) & [US8287794](https://patents.google.com/patent/US8287794).

You have probably encountered these before, but is there a consensus, or hope, that these patents don't cover a printer with a slanted Z axis like this one?

This may be a potential barrier to commercialization (and I wouldn't put it past Stratasys's lawyers to go after individuals, either).

wjsteele, 2019-04-07:
I designed this mechanism specifically to get around their patents. In both patents, claim one fails this kinematic model because we are not positioning the extruder in the XYZ space... All the rest of the claims are dependent claims, so they do not apply.

Bill

On Apr 7, 2019 5:07 PM, Milkey Mouse <notifications@github.com> wrote:

I'm not a lawyer or anything, but the main reason I didn't experiment with infinite-volume/belt-based 3D printers before was Stratasys patents US8282380<https://patents.google.com/patent/US8282380> & US8287794<https://patents.google.com/patent/US8287794>.

You have probably encountered these before, but is there a consensus, or hope, that these patents don't cover a printer with a slanted Z axis like this one?

This may be a potential barrier to commercialization (and I wouldn't put it past Stratasys's lawyers to go after individuals, either).

—
You are receiving this because you are subscribed to this thread.
Reply to this email directly, view it on GitHub<https://github.com/NAK3DDesigns/White-Knight/issues/12>, or mute the thread<https://github.com/notifications/unsubscribe-auth/ACMBQfs5nQJ4kf4XDjmZrXzbkMZkbumvks5vel4UgaJpZM4chAHH>.

NAK3DDesigns, 2019-04-07:
Thanks Bill..  I'm assuming my design is within the same constraints as yours..

wjsteele, 2019-04-07:
Yes, it definitely is.

Bill

On Apr 7, 2019 5:56 PM, NAK3DDesigns <notifications@github.com> wrote:

Thanks Bill.. I'm assuming my design is within the same constraints as yours..

—
You are receiving this because you commented.
Reply to this email directly, view it on GitHub<https://github.com/NAK3DDesigns/White-Knight/issues/12#issuecomment-480633300>, or mute the thread<https://github.com/notifications/unsubscribe-auth/ACMBQag5_uGSaJHMvgqPcegMrtEFxKubks5vemmhgaJpZM4chAHH>.

milkey-mouse, 2019-04-07:
Nice!

Closed 2019-04-07.

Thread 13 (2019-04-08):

Dimensions of printer

shaboigan, 2019-04-08:
Do you have dimensions of the fully assembled printer (not the print area) I'd like to know if this would fit in my current workshop

NAK3DDesigns, 2019-04-10:
23" W x 41"L x 28"T  or 585mm W x 1040mm L x 710mm T

shaboigan, 2019-04-10:
Thanks, let the part sourcing begin!

Closed 2019-04-11.

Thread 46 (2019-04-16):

Fusion 360 file organization

EXOgreen, 2019-04-16:
How should the files in the Fusion 360 folder be organized? For example, I found the STEP file for the 40mm blower fans on grabcad, But I don't know where to place them. I added the Bulk hardware from McMaster car to its own folder, should we have a folder for electronics, bulk parts, and 3D printed parts so that we can find what we are looking for easier? what would that structure be? LMK your thoughts.

3d-gussner, 2019-04-16:
@EXOgreen check the Development branch, we added few folders

EXOgreen, 2019-04-16:
ooooh. I was just looking in the fusion folder. Ill move bulk hardware around as well. Thanks

3d-gussner, 2019-04-16:
I think as soon we Karl is happy with the Fusion 360 files he will move this folder somewhere under Printed parts or so.

Closed 2019-04-16.

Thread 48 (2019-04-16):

Heated plate size question

3d-gussner, 2019-04-16:
Hi Karl, after seeing your 430mm high print video I was wondering why the heated plate is just 230mm long (z-axis), as a print that high would need ~335mm heated plate until it is finished.

Example:
A 430mm tall,  400mm wide and 50mm long print
- The bottom of the print would be on the heated plate up to ~330mm height
- The following 50mm height to print it would slowly move to the cold plate
- The last 50mm height to print it would be just on the cold plate

That might work for PLA but other materials may not stick anymore/loose adhesion with dropping bed temperatures and prints above 330mm may fail.

Did you choose for 230x400 because of available heating elements?

Thinking:
Terms:
- I want that the print stays on the heated plate until it is finished
- Heated plate must be 230mm x 400mm

Conclusion:
- max. print height at 45° would be ~330mm
- Y-axis travel distance of the x-axis gantry would be ~350mm
- Y-axis MGN12 Rails need to be at least ~350mm+2x 45mm(MGN12 block) =min 440mm

So I would need 2x 500mm MGN12 rails instead of 1000mm one which need to be cutted for the existing design (saving on these $50)

The travel distance of x gantry on the 500mm MGN12 y-axis rails should be around ~410 mm.
This would mean we have 60mm space for the tools of a tool changer system

NAK3DDesigns, 2019-04-17:
I haven't had any issues with prints coming off yet, but I suppose its a possibility..  How you choose to assemble yours is completely up to you(beauty of open source)..  Please make sure to share your revisions if you do..

Closed 2020-01-02.

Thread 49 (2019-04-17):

C-beam cutouts STL vs Video dimensions

3d-gussner, 2019-04-17:
Hi Karl,

I am busy to update the C-beam Fusion 360 files using your dimension from the White Knight Assembly Part 2 video.

- 5.5mm holes
  - 198mm from front
  - 342mm from front
  - 763mm from front
  - holes are 10mm from the center or 30mm + 50mm from bottom
They are bit different from the STL but don't see an issue here.

- C-beam_1 electronics cutout
  - 210mm from front
  - 335mm from front
  - and 23mm from center or 17mm + 63mm from bottom

- C-beam_2 electronics (switch enclosure) cutout
  - 240mm from front
  - 300mm from front
  - and 18mm from center or 22mm + 58mm from bottom

I have few issues/questions:
The holes on C-beam_1 are 12mm and 7mm away from the cutout, should these have same distance?

Maybe i am wrong but that looks wired to me as the "CBA_slider_tray (123mm x 35mm) " and "slide tray end cover" are sliding in the 570mm 2040 extrusions while having the 125mm x 36mm cutout not in the middle of the 4 holes.
Should it be centered as it is on the C-beam_2?
Changing the cutout to 207.5mm and 332.5mm awould center it between the holes.

On the other hand the C-beam_2 it looks good, as the Switch cutout (60mm x 36 mm) is 42mm from the holes on both sides /centered.

NAK3DDesigns, 2019-04-17:
I see what you are saying...  the weird thing is I'm checking the measurements of the prototype and they still measure out to what I listed and it appears centered..  I'm confused at this point..  I would say go with 207 and 333mm.

NAK3DDesigns, 2019-04-17:
just watched my video and it appears I did need to file down once side more than the other so I'd go with 7mm on each side..

NAK3DDesigns, 2019-04-19:
@3d-gussner you'll be happy to see I've added a Poll note to the part 2 video at 4:21 correcting the opening measurements to 207mm and 333mm..

3d-gussner, 2019-05-21:
done and pulled

Closed 2019-05-21.

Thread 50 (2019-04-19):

I could really use your help!

ludozen, 2019-04-19:
Hi there,
I really like your design of this printer! My name is Ludo, I am currently doing a graduation project at my uni in the Netherlands, in which I am trying to design a 3D printer for production of medical devices in Africa. One of the main features I want to integrate in this design is a conveyor belt system, very similar to your design, to enable continuous printing. I am about to start building a first prototype, and had some questions that I was hoping you could help me with.

Do you experience any warping issues? I can imagine that cooling of the bottom layers will cause shrinkage, and could curl op the belt. If not, how did you solve this issue? What type of belt are you using? And where did you purchase this? I am having a hard time finding the right materials. Currently I am looking into a belt made from stainless steel (0.1mm thickness).

You can also contact me by email: ludolambers@gmail.com. Or we could have a quick skype call.

I would be very grateful for any help you can offer!

Here's a picture of a very quick sketch of my current idea. I'll be upgrading a Prusa MK3.
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

Best regards,
Ludo

wjsteele, 2019-04-19:
Be careful... that specific style of printer is covered under Stratasys' patents.    Here is a quote from their patent, "In yet another example, the conveyer 104 may, by movement of the sheet 118 of material, control movement in one axis (e.g., the y-axis), while the extruder 106 moves in the z-axis as well as one axis in the plane of the sheet."  This sentence is describing the exact configuration of your proposed printer.

My way of getting around this was to alter the definition and eliminate the Cartesian requirement they imposed... i.e., XYZ positioning.  We only position in the head in the X and Y axis... Z is a "virtual" axis represented by the result of a calculation involving the requested Z as well as the physical Y axis... a value I call Z' (Z Prime = f(ZY))

Bill

________________________________
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

NAK3DDesigns, 2019-04-19:
I had some minor warping issues when I was using a thinner sheet belt, but since going to a 6mil or .15mm thick belt I haven't seem any warping yet..   I think you will find that a .5mm thick belt will be too thick.  I am then covering my belt with a custom sheet of Buildtak.  Hope this helps..  Links to both companies are below..

https://www.belttechnologies.com/
https://www.buildtak.com/

ludozen, 2019-04-19:
Thanks for your quick replies! It's a shame finding out that Stratasys' has patented this solution, thanks for pointing this out Bill.

Ah I see I made a typo, I am intending to use a .1mm stainless steel belt, not .5mm. Good to know you do not experience warping with this.

madhunm, 2019-04-22:
@ludozen check out: https://hackaday.io/project/114738-automatic-infinite-3d-printer

ArmoredBlood, 2019-04-22:
another thing to check out @ludozen is forum.beltprinters.com. I'm trying to build a community of people that want to discuss and learn more about infinite style printers.

EXOgreen, 2019-04-22:
The owner of that hackaday project is unreachable and the instructions are super unclear. This project was 1000 times more organized from day 1.  I'll have to join the belt printers forum! sounds like my kinda place. :D

NAK3DDesigns, 2019-04-22:
@EXOgreen thanks..  Though this project is better because the community and people like you are helping to make it so...

ludozen, 2019-04-23:
Yeah my interest into this type of printer was actually sparked by the hackaday project. Just like @EXOgreen, I reached out to him, with no response. Thanks for your advice guys! I digged a little deeper, and actually came to the conclusion that this type of printer might not be the best fit for the context of hospitals in Africa.

If you're interested, this is my new plan:
So the goal is to develop a low cost, low maintenance printer, that is able to have a high volume output (in terms of printed parts), with the least amount of human interference. It seems like this belt type printer will greatly increase costs, and overall challenge of the project. I have now decided to try and develop a part ejection system with less complexity, using some form of a wedge, or tool to knock prints of the bed. I'll be using Anycubic's Ultrabase bed, combined with a custom built active cooling system. My theory is that if I can cool the bed down fast enough, the parts can be pushed off with little force.

EXOgreen, 2019-04-23:
This is an idea I have seen and heard about in a few places before. It is a good starting point. A little isopropyl alcohol and compressed air should cool the bed pretty fast and not impact the print surface. Then it's a matter of creating a wall/wedge for cheep while also figuring out how to keep it from breaking parts if the parts are stuck to the build plate too much. Finally you'll need a queue system for ejection and the next job. I recommend octoprint with the print queue plugin. It allows you to specify custom end-of-print gcode for bed ejection and then starts the next job.

NAK3DDesigns, 2020-01-02:
Closing due to over 6 months of inactivity..

Closed 2020-01-02.

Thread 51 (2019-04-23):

Drip tray rework..

NAK3DDesigns, 2019-04-23:
Hi Guys, I had to make a change to the Build Plates see (v3) basically I offset the center 400mm area to the right.  By doing this the drip tray will now be too small to fill the void between the main 4080 extrusion and the buildpate..    I'm currently busy getting a mockup kit pieced together for PS to use for sourcing kit components and creating assembly instructions.  If anyone want to take a crack at stretching it out 5mm more, I'll test fitment one I receive the newly cut plates..  If you look at it from the top it should just be a matter of carrying the diagonal edges out 5mm further..  If there are any question let me know..

EXOgreen, 2019-05-15:
Can you post a picture of the area you are talking about? I'm not too familiar with where all the parts fit when its all assembled.

NAK3DDesigns, 2019-05-15:
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

here is a pic of the drip tray.. the area marked out in red would be the new size..  basically going 5mm further into the plate.  I have shifted the buildplate 5mm to one side to allow for a larger off belt area.

EXOgreen, 2019-05-16:
ok, that makes sense now. I'll get that updated. And maybe see if its angle is the same in both cad designs.

NAK3DDesigns, 2019-05-16:
awesome.. thanks

EXOgreen, 2019-05-16:
see pull request #52 and let me know if it needs work

EXOgreen, 2019-05-20:
@NAK3DDesigns just confirming you saw this

NAK3DDesigns, 2019-05-20:
Yes, I did.   Sorry just had a crazy weekend.

NAK3DDesigns, 2019-05-25:
just merged the request..  hopefully here soon I'll get time to start test printing all these fusion files...  Thanks again..

NAK3DDesigns, 2020-01-02:
Done!!!  Closing ticket

Closed 2020-01-02.

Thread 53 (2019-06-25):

Kits?

paulbuzzby, 2019-06-25:
Hi, This is probably the wrong place to ask but I saw somewhere about kits being made for this. Not only am I keen to acquire a kit with all the non-3D printed I would be extremely interested in helping out either sorting or helping to distribute these. I live in the UK and I know that shipping from the US is just eye-watering expensive to elsewhere in the world.

Paul

NAK3DDesigns, 2019-06-25:
Hi, thanks for your interest in my design.   I would recommend contacting Printed Solid directly as they are going to be producing the kits.

paulbuzzby, 2019-06-25:
Thanks,

A different question along the sames lines. Has anyone put together places outside of the US that the Non-3D printer parts can be ordered?

NAK3DDesigns, 2019-06-25:
Yes, I believe ScaldaYT has pieces together a UK source list.

NAK3DDesigns, 2020-01-02:
*******UPDATE*******
I was just informed that due to legal reasons Printed Solid will NOT be producing kits nor will they even be able to carry the belt materials..  They do plan on building a White Knight group on the main page that will contain all the parts that they carry used in making a White Knight..

Sorry for the bad news..

wjsteele, 2020-01-03:
Legal reasons? Do they think there is IP stopping it?

NAK3DDesigns, 2020-01-03:
I don’t know all the details but I was told their patent lawyers advised against it.

peacho17, 2020-01-03:
I am currently working on a version that uses industrial strength aluminium foil for the bed rather than the belt. Could this bypass the patent infringement concearns?

It works out way cheaper too. The foil is near 1mm thick and is $10 for a roll 45cm wise and 30m long.

Regards
Mark Pietsch

Sent from my iPhone

On 3 Jan 2020, at 11:19 am, NAK3DDesigns <notifications@github.com> wrote:

I don’t know all the details but I was told their patent lawyers advised against it.

—
You are receiving this because you are subscribed to this thread.
Reply to this email directly, view it on GitHub<https://github.com/NAK3DDesigns/White-Knight/issues/53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>, or unsubscribe<https://github.com/notifications/unsubscribe-auth/AK7OEEHVH6YZVT76NXUG6OLQ32AA5ANCNFSM4H3IF2DQ>.

NAK3DDesigns, 2020-01-03:
I'm not certain where the patent infringement concerns are but I'm guessing any printer that prints on a belt would be the issue..
    Also with the aluminium you may have issues with it stretching and curling..  that is the reason why I use fully hardened stainless steel..  I tried cheaper stuff before and had that issue.

Closed 2021-03-23.

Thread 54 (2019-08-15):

Request:  Update the main Readme file with a list of printer capability specs

quarky42, 2019-08-15:
When you have time, would you please update the main Readme file to include a rundown of the various specs to include (but not limited to):

Layer Height Range (min to max)
Build Volume
Min and Max Travel Speeds
Filament Size
Max Bed Temperature
Max Hot End Temperature
Overall Weight
Overall Dimensions
Anything else you can think of that would be neat to see at a glance?

I've gotten the answers to many of these things from various places, but it would be nice to have them all in one spot (and to verify what I've heard in videos and pulled from other places is correct.)

Johannp02180, 2020-03-25:
I think it would help if you answered your own question and posted the specs you found and then he could easily verify them. Also, a lot of the specs depends on what hotends you buy and bed. You could easily lookup the hotend he used and find the max temp.

quarky42, 2020-03-25:
I had a suggestion for how the information available could be improved.  He could take it or leave it.  I wasn't trying to waste his time any more than necessary having a discussion about it.  Me guessing at the parameters when he should be familiar with them isn't helpful.

Perhaps if you had lead by example I'd see better what you're talking about.  A couple of obvious parameters don't address the specifications as a whole being lacking.

Johannp02180, 2020-03-25:
I see, if you watch the video by 3Dprintingnerd, you'll see even he himself isn't 100% on the specs, cause he hasn't tested the printer to its limits yet. I apologize if my previous comment came down hard.

quarky42, 2020-03-25:
Thank you for reconsidering your tone.  I did take it as pretty aggressive, but if it wasn't meant as such then I can accept that I was mistaken.

Yes, I did notice that he wasn't sure in that video but then in a later video he tests it and gets pretty close to the limit. That was 7 months ago.  I had hoped that at some point he'd consider adding the information.  Even if it wasn't complete at first, it could always be added over time.

I figure the creator was the best place to start rather than trying to piece it together and guess.  I was particularly interested in the whole step positional accuracy vs the microstep accuracy.  Those two parameters would have been interesting to see.  Even if I had to calculate the effect of the triangular ZY axis on it, it would be neat to see how it compares to some other systems.

Johannp02180, 2020-03-25:
Yeah I agree it would be great to have that info and I didn’t mean to be aggressive. I was just thinking that having your info would be great for other users out there.

Sent from my iPhone

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

NAK3DDesigns, 2020-03-25:
Lets all play nice... ;) Sorry I haven't made any updates on the info requested but to be honest I'm not sure of the best ways to benchmark the printer to give accurate numbers.. Can it move at over 100mm/sec sure but at what loss of print quality, I do most of my prints at 30mm/sec with moves at 120mm/sec.  I've used nozzles from ,4 to 1.0 succesfully  but am still dialing in settings...  Sadly this is just a side hobby for me and I have many other projects I'm trying to work on as well..  To be honest I was kinda hoping I would publish what I had and the community would start building and improving my design because like I said it isn't perfect..  For example I've already given up on using the bowden design of the White Knight and switch mine over to a direct drive setup like I put on the Squire because I wasn't able to get a working slicer profile that eliminated the pressure feedback issues associated with such a long bowden run..

Sorry this turned into a bit of a rant..  I'm just not a highly technical guy..  I'm good mechanically and decent with firmware and settings but I'm no Chris Riley with all the in depth details..  I may have gotten lucky that it works at all.. lol

quarky42, 2020-03-25:
I don't think you give yourself enough credit.  Maybe focusing on the kinematics and documenting them isn't the fun part, but it's clear you have a good eye for detail otherwise you wouldn't have had the success you've had.   There is no luck in complex system design.  There are just variables and managing those variables, and you've done a great job.

You highlighted a really important issue about movement speed.  A fair spec would be to say both normal print speed range and normal fast travel speed.  If the system allows for 120mm/s travel then print speeds over 30mm/s are possible with the right cooling and slicer settings.   As a baseline 30 and 120 are good data points.

What does 1 full step of the stepper motor equate to in movement in X?  How about it. ZY?  This info could inform layer height choices.

I'm not familiar with the squire.  I haven't caught up on the latest videos.  If I were building a similar setup to the White Knight, I'd be inclined to use the remotely driven / direct drive Zesty Nimble extruder.  That gets the weight of the motor off the moving carriage so less momentum but still direct driven through a torque cable.  What did you do on the squire?

NAK3DDesigns, 2020-03-25:
Thanks,
I think a lot of the info you are looking for is contained with in the Config.g file of the duet configuration..
 https://github.com/NAK3DDesigns/White-Knight/blob/master/Duet%20Config%20Files/sys/config.g

Current micro-stepping is set at 16x and config is as follows..  X=160, Y=160, & Z=208.75 so in full steps that would be X=10, Y=10, Z=13.047..

On the Squire I moved the Bondtech BMG and a pancake stepper to the top of the extruder carriage with approx 150mm of bowden between them..  I'm told it is similar to how the Prusa is set up.

I haven't really done any videos on the Squire yet (kind got burned out doing all the videos for the White Knight)  Joel did do an interview at ERRF where I covered most of the changes.  Here is the link to my portion of the interview.. https://youtu.be/bekwCnl9BwY?t=1343

Hope this helps a bit..

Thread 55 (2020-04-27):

Belt Group Buy

JoshuaMorris, 2020-04-27:
Hi,

[Tj says he's done leading the group buys](https://infinityprinters.org/t/group-buy-endless-belt/67). I missed the last one and am willing to lead a group purchase to get a pair myself. If you're interested in joining in, comment on this issue and we can group up. I will keep this issue updated as we get enough people.

Quoting this info from the other group buy as the pricing/shipping arrangements will likely be the same:

```
Okay pricing for the white knight belt:

1 Belt: $450
2 Belts: $400 each
3 Belts: $355 each
4 Belts: $325 each

There is also the price of shipping which is from them to my address and then from my address out to you.
```

wjsteele, 2020-04-27:
I'm up for two!

madhunm, 2020-04-27:
@JoshuaMorris I would like one set please

sorren4, 2020-04-28:
How low does it go based on volume?  Is the pricing tiered?

AzonicTech, 2020-04-29:
I would like to get 2 of them. Is anyone putting together an excel sheet that we can add our name to? The one on the link will not let me add my name.

reFlex-lab, 2020-04-29:
I think it's already too late

Le mer. 29 avr. 2020 à 15:25, AzonicTech <notifications@github.com> a
écrit :

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

JoshuaMorris, 2020-04-29:
@AzonicTech @reFlex-lab I'm working on setting up a group buy, I will be putting together a form/spreadsheet once I collect from everyone who wants to join me in doing a purchase. I'm just waiting a little to allow for other who might be interested in joining in.

spyle, 2020-05-15:
I'm interested too. I'm just now looking into building one and I really think I want the Squire. Are the belts used the same size on the squire and white knight?

NAK3DDesigns, 2020-05-15:
> I'm interested too. I'm just now looking into building one and I really think I want the Squire. Are the belts used the same size on the squire and white knight?

No, the Squire belt is almost half the size of the white Knight belt.

spyle, 2020-05-15:
@NAK3DDesigns Wheres the best place that I can bug you or a group with some questions?

NAK3DDesigns, 2020-05-15:
> @NAK3DDesigns Wheres the best place that I can bug you or a group with some questions?

NAK3DDesigns@gmail.com   First question is free additional are $5 per.. lol just kidding

cr10guy, 2020-05-19:
How do I sign up to buy I’ll take 4

JoshuaMorris, 2020-08-06:
After some consideration, this doesn't seem feasible for me to facilitate a group buy. I cannot at this time handle the redistribution of belts to everyone that wants to be a part of it. I would only be able to help those folks who could come and pickup their belts in person (Sacramento, CA).

tbedore, 2020-12-08:
@cr10guy not sure if you bought a belt or not but the pricing doesn't go down much from 4 belts i'd suggest for you to just buy the 4 yourself. And to everybody else I was the one who coordinated the first 2 group buys. They aren't really feasible unless you are driving to pick it up. For the belts, you pay for the belt in addition to the shipping cost from belt technologies to the person who is re-shipping them. Those boxes are not that small, 20x20x20 boxes, so you're paying for the repacking costs. And then on top of that the person who is coordinating the group buys, I did them through invoicely and square payment services. Those take a small percentage for using their services. So when looking at the price given to you by me, it is belt+shipping (belt to me) + shipping (belt to you) + shipping materials + CC processing fees. I looked at the numbers and after all of that, depending on your location will determine how close it is to price from belt technologies. I get away with some dirt cheap shipping, but they are located in MA. I would be willing to do another one if anybody is interested but I'm just putting this out there and being upfront about it.

tbedore, 2020-12-08:
Important to note also, buying 2 different size belts will not make the price go lower. The price per belt goes down because of their initial setup costs ($220 per size), so when the price per belt goes down that is solely because that initial setup cost is being split across all the belts. But say you got a squire belt and a white knight belt, you are paying for the setup cost on both of them, it doesn't get tiered together. You can reply to me here, or shoot me an email at ntwyoutube@yahoo.com i'd be more than happy to discuss purchasing belts.

-TJ

tbedore, 2020-12-09:
If anybody is interested in another group buy of the belts, please keep in mind what I have said above, take a look at the [blog post I made on the infinity printers forum](https://infinityprinters.org/t/group-buy-endless-belt/67/51?u=tj_bedorel) and if you are interested after all of that feel free to add your details to the [google sheets](https://docs.google.com/spreadsheets/d/1kebBYrp085TU6l2bKg5meDZd1eZV_KM43DCM--KY5J4/edit?usp=sharing) that I have created . Happy Building

-TJ

Helvensteijn29, 2021-03-01:
Hi tbedore, kan i still sing up for a belt?

NAK3DDesigns, 2021-03-23:
Closing issue..  Please open a new ticket for each group buy and close the ticket once the group buy closes.

Closed 2021-03-23.

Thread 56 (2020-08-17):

Silicone Heater designation

BaronPhartman, 2020-08-17:
Hello,

I was looking through the BOM of the White Knight, and tried to find the silicone heater used with the info that's present and couldn't find anything, would it be possible that rather than a ebay number, you could post the dimensions and voltage/wattage of the heater itself?

Thanks so much.

NAK3DDesigns, 2020-08-17:
I just checked and the listing is still valid.  Literally all you have to do is copy and paste the item number in the e-bay search window and the listing comes up..  here is the link: https://www.ebay.com/itm/8-X-16-200-X-400mm-24V-250W-w-3M-w-104GT-thermistor-at-center-Printer-Heater/143206149832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

Closed 2020-08-18.

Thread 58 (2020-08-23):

Question Conveyor Belt

jedisintraining3, 2020-08-23:
Could we use other types of cheaper conveyor belting like this pvc one here: https://www.dhgate.com/product/perimeter-900x200x1mm-customized-pvc-white/533630499.html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

And maybe put custom long buildtak sheeting on the conveyor belting.

Almost like this guy did: https://www.youtube.com/watch?v=aF0wnY1v0Pk

Just an idea, would make this project much more affordable

Cheers,
Aidan Villacampa

NAK3DDesigns, 2020-08-24:
I'm sure it's possible..  I can't say that I've tried every kind of belt
(I'm too poor to do that. lol)  I encourage everyon eto try anything they
think might work..  For example i would have never thought the belt on the
CR-30 would have worked as good as it does..  I'm sure they may still be a
better option out there but until more people experiment who knows..

Karl Brown
NAK 3D Designs
Youtube: youtube.com/c/NAK3DDesigns <https://t.co/Wi7S9iGhtI?amp=1>
Twitter: https://twitter.com/NAK3DDesigns

On Sat, Aug 22, 2020 at 8:44 PM jedisintraining3 <notifications@github.com>
wrote:

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

HasslerEngineering, 2020-10-18:
@NAK3DDesigns Do you know what belt the cr30 is using?

NAK3DDesigns, 2020-10-18:
Sorry no, I don't know the exact composition or source of the belt Creality is using...  I'm hoping in the future they will release the source and details.

HasslerEngineering, 2020-10-18:
Ok. What thickness Are these stainless steel belts you are suggesting?

NAK3DDesigns, 2020-10-18:
6 thousandths of an inch or .15mm

HasslerEngineering, 2020-10-19:
Thank you very much!

Closed 2021-03-23.

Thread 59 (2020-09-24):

Source: Thermal Isolating Washers?

Hvest3, 2020-09-24:
Hey Karl!

I'm curious as to where you sourced your thermal isolation washers for the hot and cold plates.  I apologize if you've covered this elsewhere, but I couldn't find them in the BOM.

Thanks man!

NAK3DDesigns, 2020-09-24:
The smaller ones that go above the heatplate are

M5 high temp washers | 10 | McMaster-Carr | 93785A214

As for the larger 15mm OD washers I used some G10 like this
https://www.ebay.com/itm/G10-Sheet-Knife-Handle-1-8-x-5-x-11-7-8-RHINO-GREY/114295707394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
and then used a hole saw with a 5mm center bit..

Hvest3, 2020-09-24:
Ahhh, G10, that makes sense.  I already had the PEEK M5 washers, but that clears up the mystery. Thanks man!

Closed 2020-09-24.

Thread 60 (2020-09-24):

Source: Hot/Cold Plate Machining

Hvest3, 2020-09-24:
Hey Karl,

Curious as to who you used to machine your hot/cold plates.  Been having trouble getting someone to do it without technical drawings and that's well beyond my CAD expertise.

Any recommendations you can offer are greatly appreciated.  Thanks man!

NAK3DDesigns, 2020-09-24:
To be honest unless you really want the very clean cut look you could just have the plates precut to the outer dimensions and do the cutouts with a jigsaw and drill the holes with a hand drill..  Otherwise the STEP or F3D files should be good enough for mist shops..  Sadly I had my plates waterjetted by a friend that doesn't work at the same shop anymore..

Hvest3, 2020-09-24:
Helps to have friends in a CNC shop for sure!  I'll keep searching for someone who can do it from the STEP files.  Appreciate the help and the quick reply!

Closed 2020-09-24.

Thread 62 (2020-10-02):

Question: Squire CBA Tray

Hvest3, 2020-10-02:
Hey gang,

I'm trying to squeeze a solid state relay into the Squire CBA tray to no avail, so I figured I'd have a go at modifying the slide tray design to accommodate one.  However, when I pull up the tray parts 1 and 2 in Fusion 360, they seem to start with a pretty finished design that's then tweaked and cut in half.  Is there a version available that I can use to fundamentally tweak to make the whole assembly longer?

Or am I just doing it wrong?  I'm certainly a novice at modeling so feel free to point me in the right direction :)

Hvest3, 2020-10-06:
Figured it out! Turns out I was just doing it wrong...lol

Closed 2020-10-06.

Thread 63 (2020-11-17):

some STL-files can't be downloaded

LDekor, 2020-11-17:
Hi. i have trubble downloading some stl files. something that can be fixed?

these are the files that cant be downloaded:

2-Roller_Insert.stl

2-Side_Support_Bottom_Brace.stl

3-Pulley_Bearing_Mount_V2.stl

1-Peeler.stl

NAK3DDesigns, 2020-11-18:
I've re-loaded all of the files and they appear to be working now..  If you have any future problems try downloading using the desktop app..  It seems to work more reliably..

LDekor, 2020-11-19:
thank you. i am planing on building your printer. i have one question. how many parts do i have to make of the diferent printed parts? is it just one of each?

NAK3DDesigns, 2020-11-19:
the number at the beginning of the file name is how many you need to print..  i.e. **2**-Roller_Insert.stl   so you print 2..

Closed 2021-03-23.

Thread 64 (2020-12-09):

Group Buy On Belts

tbedore, 2020-12-09:
Hello Everybody,

My name is TJ and I have been the person who has pretty much coordinated (to my knowledge) the group buys for the belts on the printer. I'm running another one again as I have more free time than I would like to admit, so here we go. This time I am being up-front with you about everything that goes into a belt purchase for the group buy. I am copying and pasting everything that I wrote yesterday on the[ Infinity Printer's Forum](https://infinityprinters.org/t/group-buy-endless-belt/67/51?u=tj_bedore) for sake of not repeating myself and making sure to get the entire information there.

Message:
I wanted to thank everybody once again for participating in our group buys. I wanted to put this out there because I’m willing to do it again, with the current situation I have a large amount of free time on my hands and would be willing to set up another buy if anybody is interested.

I’m going to be completely transparent about everything just so you as a consumer know what your options are and how everything works for this.

So when you ask to participate in the group buy you add your name to the spreadsheet, that spreadsheet stays available usually for about a month or so and then once we get close to me closing it I reach out to everybody to make sure they are still in for the price of the belt.

Once that is confirmed I reach out to Scott over at Belt technologies and he helps me setup the invoice and I get the price per belt.

The price that I relay to you includes all of this in the amount:

Price for the belt given to me by belt technologies
2% CC fee charged by belt technologies
Shipping fee from belt technologies to me
Shipping materials fee for shipping the belts to you (20x20x20 box)
Shipping Fee for the belt from me to you
CC processing fee charged by the company I use for invoicing (2.9% + 0.30 flat fee)

That’s a lot and in my opinion, the way this works out the best for you is if you are local to me and you come and pick up the belt, that way there are no shipping materials necessary and gas is usually cheaper and shipping providers.

I’m in Essex county in Northern NJ. Again completely transparent also, I’m an 18-year-old senior in High School, but you can trust me as I have done similar things to this numerous times.

If you have any questions about this, or interested in me setting up another group buy, you can reply to me down below. You can shoot me an email at ntwyoutube@yahoo.com (I usually reply pretty quickly and if not within 24 hours), or send me a message through the issues section on the Github that is located there too.

To note also, I am building my squire in a series of live-streams on my YouTube channel: https://www.youtube.com/c/ntw3d. If you ever want to talk there I usually do a stream once every other week or so, we can talk about belts there.

Again I do these belt purchases to help you guys out a little bit, I usually add about $20 onto each belt purchase because coordinating the purchase of these takes a lot of work, so I need to get a little something out of all of this. Unlike the first one I'm not actually participating in the buy.

If you are interested in joining the group buy please add your details to the [google sheet](https://docs.google.com/spreadsheets/d/1kebBYrp085TU6l2bKg5meDZd1eZV_KM43DCM--KY5J4/edit?usp=sharing) and I will reach out to you later on down the road when I will begin to collect payments to make sure you are still willing to get this belt.

Stay safe and happy building

-TJ

tbedore, 2021-03-23:
Group buy has concluded. I'll be going to college next year so this will be the last one run by me. Good luck all and happy printing!

Closed 2021-03-23.

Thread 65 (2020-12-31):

Interests in Partial Kits?

tbedore, 2020-12-31:
Hello,

I was wondering if anybody would be interested in possibly a frame kit from LDO Motors that is already cut down to spec for the white knight and with all the holes drilled in all the extrusions, holes cut, ends tapped, etc. You will probably still need to drill and tap the holes for the linear rails as that is different for everybody unless I could manage to get LDO to do that but I doubt they'd be willing to.

There is a very high likelihood that I would be able to get a motor kit from LDO also with everything that we would need. They wouldn't need to have connectors on them we could do just plain wires on the end all prepped for soldering later on with the wiring.

I could also probably get the linear rails cut down to size from them with the blocks and everything and have that all in one kit.  I want to see if anybody would be interested in any of these kits. Again the same idea with the fees and everything.

LDO -> Me
Me -> You
CC processing fee from Paypal

I would like to know if anybody would be interested in this.  If you are please add your name to the [spreadsheet](https://docs.google.com/spreadsheets/d/1zxAisEYr6v_wFz1Z-v1xb3HcQ-9nKwCt-PpczsmUoD8/edit?usp=sharing) and select from the dropdown what you would be looking for. I'm going to send an email to Jason over at LDO and see if he would be willing to do anything like this.

StumbleNOLA, 2021-01-28:
Honestly I would be much more interested in being able to buy a working machine for a premium over the cost.

servant74, 2021-01-29:
Agreed

On Thu, Jan 28, 2021 at 4:52 PM StumbleNOLA <notifications@github.com>
wrote:

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

--
><> ... Jack

If you are not paying for something, you are not a consumer, you are the
product. - Chamath Palihapitiya

"Tell me and I forget. Teach me and I remember. Involve me and I learn." -
Ben Franklin

VinnyCordeiro, 2021-01-29:
A working printer would be nice, but I'd buy even a full kit in a box if that save me the time to chase all the components.

Closed 2021-03-01.

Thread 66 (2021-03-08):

Multinozzel for Beltprinters

Prototyp-L98, 2021-03-08:
Hello everyone,

im building on my own version of a Beltprinter with 4 Nozzels.

But the problem is that neither CrealityBelt or CuraBlackbelt have multinozzel
for Beltprinter support. Dont get me wrong its work perfectly fine with "normal"
Printers but not for Beltprinters.

If u cant imagine what i mean i added my Fusion Hotend build.
[Belthotend.zip](https://github.com/NAK3DDesigns/White-Knight/files/6103319/Belthotend.zip)

NAK3DDesigns, 2021-03-09:
I suggest contacting Stewart at Kiri:Moto   - sa@grid.space    He has been working on a beta belt slicer and has been very eager to add functions as they are requested..  He thinks the current configuration will work.  Here  is the link to it..  https://grid.space/kiri/

Prototyp-L98, 2021-03-09:
Thank you very much that helped a lot.
I never heard of this Slicer but it looks very promising.
I'll get right on testing.
Thank you

Closed 2021-03-09.

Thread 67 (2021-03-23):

Device buyers

SeyedAli1998, 2021-03-23:
Hi Karl
Has this device model ever had buyers?
If so, who bought it and who needs it?

Thank you in advance for your answer
SeyedAli

NAK3DDesigns, 2021-03-23:
This isn't something you buy as a kit or assembled..   This is just a repository of all info needed to build your own.  As such I really don't have any info as to how many people have bought it or built it.

SeyedAli1998, 2021-03-23:
Thank for your reply.

Closed 2021-03-23.

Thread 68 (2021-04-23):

Blackbelt cura

LDekor, 2021-04-23:
Hi. i downloaded the firmware some months ago but have not tried the firmware befoure now. the program crashed when choosing nozle so i deleted the program. now i cant find blackbetl 3.6.0 and the update because they only hav the new 3.6.2 program. what shoud i do to make this work?

- Thomas

NAK3DDesigns, 2021-04-23:
Hi, To be honest Blackbelt Cura is very out of date, at this point I recommend downloading IdeaMaker..
https://www.raise3d.com/download/
Then I'd recommend downloading one of the CR-30 profiles and just adjust the machine dimensions as I used my White Knight setting to build the original CR-30 profile.
https://www.ideamaker.io/

GpMissi, 2021-04-25:
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

Hi, I'm doing some simulations to evaluate the project. Slicing with Ideamaker I see that it is unable to recognize bridges, is there a solution for this problem? Thank you

(sorry my english, i use google translate)

GpMissi, 2021-04-25:
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

NAK3DDesigns, 2021-04-25:
Sorry maybe it's the translation but I don't see the problem..

Karl Brown
NAK 3D Designs
"The possibilities are Infinite"
Youtube: youtube.com/c/NAK3DDesigns <https://t.co/Wi7S9iGhtI?amp=1>
Twitter: https://twitter.com/NAK3DDesigns

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

GpMissi, 2021-04-25:
I try to explain my concern. As you can see from the image, the thread of material will be extruded as a normal filling and not as a bridge, this means that it will not go to an increased speed and the ventilation provided for the bridges will not be activated.

GpMissi, 2021-04-25:
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

riempimento solido = solid fill

Ponte = bridge

NAK3DDesigns, 2021-04-25:
oh ok, sorry I don't know anyway to fix that, you can try contacting
ideamaker and open a trouble ticket..  admittedly I haven't had much
problem with bridging though..

Karl Brown
NAK 3D Designs
"The possibilities are Infinite"
Youtube: youtube.com/c/NAK3DDesigns <https://t.co/Wi7S9iGhtI?amp=1>
Twitter: https://twitter.com/NAK3DDesigns

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

GpMissi, 2021-04-25:
OK thanks. I will try to contact Ideamaker technicians :-)

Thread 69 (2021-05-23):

Belt

GpMissi, 2021-05-23:
I would like to order the belt from Belt Technology UK, could you give me the characteristics that the material must have? Thank you

NAK3DDesigns, 2021-05-23:
Here is the spec sheet belt technologies sent me.  You need to order it in the "Full Hard" grade,   .006" thousandths thick.
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

GpMissi, 2021-05-23:
Thanks so much. Do you think this belt is ok or would you ask Belt Technology for different characteristics? Where would you like to improve your project? I am obviously talking about the belt printing bed section.

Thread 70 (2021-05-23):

Belt

SeyedAli1998, 2021-05-23:
Hi Karl
Doesn't the belt slip on the rollers?
and
Why is the plate under the belt an aluminum plate?

NAK3DDesigns, 2021-05-23:
With the proper tension the belt will not slip.  I chose and ATP5 cast aluminum plate because since it is cast it won't warp as easy, its milled perfectly flat, it would be lighter than steel, and it is a good conductor of heat.

SeyedAli1998, 2021-07-26:
Hi Karl

SeyedAli1998, 2021-07-26:
Hi Karl
What's the plastic material you used over the steel belt?
Is it a Neoprene Rubber Sheet?
Can you help me about it?

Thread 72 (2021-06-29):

Parts list

Gigas-E, 2021-06-29:
Hi I'm very interested in building my own white knight and I am needing a parts list so I can start buying the plethora of parts required.

Thank the Lord I was blessed to get in on the belt group buy and already have the hardest part to get. All I require now is the rest. I trued to find a parts list with no success. If it's not too much trouble for you could you also include where you were able to source each piece I would be so grateful!!

Thanks for creating this awesome 3D printer!!! God Bless!

NAK3DDesigns, 2021-06-29:
You are already in the correct place..   everything you need to know is here in the github..  https://github.com/NAK3DDesigns/White-Knight/tree/master/BOM

midippel, 2021-06-29:
Hey @Gigas-E, I was going to be building the squire, but just had my first kid and don't really have time for this right now. I have everything already together if you'd be interested in buying it as a kit(minus the squire specific stuff). Email me at midippel@gmail.com

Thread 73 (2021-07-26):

belts plastic

SeyedAli1998, 2021-07-26:
Hi Karl
What's the plastic material you used over the steel belt?
Is it a Neoprene Rubber Sheet?
Can you help me about it?

wjsteele, 2021-07-26:
His is covered with a custom BuildTak surface.

SeyedAli1998, 2021-07-26:
> His is covered with a custom BuildTak surface.

Don't you know the material name?
Unfortunately I couldn't buy from BuildTak

wjsteele, 2021-07-26:
You'd have to ask BuildTak for their material.On Jul 26, 2021 6:51 AM, SeyedAli1998 ***@***.***> wrote:

His is covered with a custom BuildTak surface.

Don't you know the material name?
Unfortunately I couldn't buy from BuildTak

—You are receiving this because you commented.Reply to this email directly, view it on GitHub, or unsubscribe.

SeyedAli1998, 2021-07-26:
> You'd have to ask BuildTak for their material.On Jul 26, 2021 6:51 AM, SeyedAli1998 ***@***.***> wrote: His is covered with a custom BuildTak surface. Don't you know the material name? Unfortunately I couldn't buy from BuildTak —You are receiving this because you commented.Reply to this email directly, view it on GitHub, or unsubscribe.

thank you

paulmn-web, 2021-08-01:
I custom built my belt on the printer bed - in essence the bed is an ideal set up for making laminate belts. I have a compression roller temporarily on the rigid portion of the bed, the first laminate layer is tape tacked together and then the layers are laminated onto that. Offset the laminate ends and I used Selley’s horizontal contact adhesive which is temperature stable to 130’c.
Mine’s a 3 layer laminate with fibreglass or stainless mesh core depending upon non heated or heated bed. Experiment with whatever flexible sheet material you have locally for your top surface, the best is what is best for your specific applications - hence I have heated and non heated belt for different parts. Try a piece in your standard 3d printer and see what works.
I am now building a larger one with dual extruders - my application requires a carbon fibre reinforced Petg skin for strength and the foaming pla core material to reduce weight. It therefore copes with a non heated bed nicely. The carbon fibre minimises warping and the petg sticks well to the belt. The pla sticks well to the petg. The foaming pla gives a nice finish - shame it’s hidden inside.
The required printed part size is 1600 x 420 x 160 - so a 500mm belt width minimum. The 1/3 scale prototype worked well so fingers crossed on the full scale.

Sent from my iPhone

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

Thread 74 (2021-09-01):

Cr30 profiles for black belt

123ccv95, 2021-09-01:
Hi from Chile, i'm currently starting to use the cr30... I've seen that people reccomend yours profiles for the cr30 but haven't been able to find it, Do you know where can i download this profiles ?

NAK3DDesigns, 2021-09-01:
Hi,
Most people are probably referring to my ideamaker profiles.  Blackbelt
Cura is severely out of date and updates are rare.  here are links to
ideamaker and my profile.

https://www.raise3d.com/ideamaker/
https://www.ideamaker.io/detail/1675-cr-30

Also there is a web based slicer called kiri:moto.  the developer is a
CR-30 owner and he is constantly (almost daily) making improvements.  Here
is a link to that as well.

https://grid.space/kiri/

best of luck

Karl Brown
NAK 3D Designs
"The possibilities are Infinite"
Youtube: youtube.com/c/NAK3DDesigns <https://t.co/Wi7S9iGhtI?amp=1>
Twitter: https://twitter.com/NAK3DDesigns

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

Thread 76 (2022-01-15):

Ordering parts from Printed Solid

Vordir, 2022-01-15:
There are a few parts in the BOM I have a Problem with

- Duet Wifi = There is only the new version "Duet2Wifi" available, but i red thats not a problem. is that right ?

- Mosquito Mount = is not available. but i saw in the CAD that this would be a "Groove Mount Bowden Adapter"
   https://www.3djake.de/e3d/groove-mount-bowden-adapter ?

-Slice Thermistor = there isn´t stated which one i need. when its the "SLICE ENGINEERING HIGH TEMP THERMISTOR"  is it the availible "RTD PT 1000" for 50$ or would the 300°C version OK ? but this ins´t available either. is there an alternative ?
   https://www.printedsolid.com/products/slice-engineering-high-temp-thermistor-1

-Silce 50W heater = is it the "SLICE ENGINEERING 50W HEATER" in 12 V or 24 V version ?
    https://www.printedsolid.com/collections/all/products/slice-engineering-50w-heater?variant=12533493989461

-LDO .9 Stepper = there is no such stepper on the website.  I only found this : https://www.ebay.de/itm/333367708304
   I dont know much about electronics. chose this project to learn something about it, but dont want to order the wrong parts

-Nema 17 5.1 geared stepper = on the stated website not found. found only 5:1 geared here https://www.ebay.de/itm/392172201987
                                                    is that right ? is there an alternative

Thanks in advance
Yours sincerely Daniel

NAK3DDesigns, 2022-01-15:
Yes, the Duet2Wifi is what you want.
I believe I used the 300°C
As for the heater if you go with the recommended 24V power supply then you need the 24V heater cartridge

Attached is an image from the printed solid shopping cart showing the 5:18 Geared stepper, the .9 steppers and the slice Mosquito groove mount.

Hope that helps

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

Vordir, 2022-01-17:
helped a lot, thanks :)

Closed 2022-01-17.

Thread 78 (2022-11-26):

3d printer

Ladyshakti, 2022-11-26:

Ladyshakti, 2022-11-26:
I can load the file into fusion 360 on my Android phone to see the instructions

Ladyshakti, 2022-11-26:
I can not load the file. I've downloaded the file in assembly for fusion 360 but it doesn't load. When I try other programs it says there is an character error on line 1.  I want to see the measurements for frame and what goes where. I also need it for roller including the extra space between belt and frame. If I can get this I can work out the new measurements for the print size I want. 1000mm height and 1500mm wide.  I am not looking for free advise and waste your time.  I intend on paying for your experience

tobitus, 2022-12-08:
Clicking "save as" on the file link doesn't work in github.

Here's how to view the file in fusion (this is on desktop):

go to this page:
https://github.com/NAK3DDesigns/White-Knight/tree/master/Assembly

Hover over the link "White Knight Full Assembly v126.f3z" and you will see a check box pop up to the left.
Click on the checkbox so it turns blue.

Now look on the bottom right of your screen and you will see a black arrow pointing down.  Click that arrow.
-github will download the correct file.

no open this file from fusion and it will import all the pieces like it is supposed to.

MR-lwj, 2023-01-27:
Excuse me, Sir, I am a 3D printing enthusiast from China.I want you to know some questions about the control board of this printer. May I ask what type of motherboard you have?

NAK3DDesigns, 2023-01-30:
> Excuse me, Sir, I am a 3D printing enthusiast from China.I want you to know some questions about the control board of this printer. May I ask what type of motherboard you have?

It uses a Duet Wifi.  All components used are listed in the BOM.

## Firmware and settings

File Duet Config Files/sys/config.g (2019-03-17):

; Configuration file for Duet WiFi (firmware version 1.21)
; executed by the firmware on start-up
;
; generated by RepRapFirmware Configuration Tool v2 on Sun Nov 25 2018 19:09:02 GMT-0500 (Eastern Standard Time)

; General preferences
G90                                          ; Send absolute coordinates...
M83                                          ; ...but relative extruder moves

M667 S1                                      ; Select CoreXY mode

; Network
M550 P"White_Knight"                         ; Set machine name
M552 S1                                      ; Enable network
;M587 S"SSID" P"Password"                     ; Configure access point. You can delete this line once connected
M586 P0 S1                                   ; Enable HTTP
M586 P1 S0                                   ; Disable FTP
M586 P2 S0                                   ; Disable Telnet

; Drives
M569 P0 S1                                   ; Drive 0 goes forwards X
M569 P1 S1                                   ; Drive 1 goes forwards Y
M569 P2 S0                                   ; Drive 2 goes backwards Z
M569 P3 S0                                   ; Drive 3 goes backwards E
M350 X16 Y16 Z16 E16 I1                      ; Configure microstepping with interpolation
M92 X160.00 Y160.00 Z208.75 E814.62          ; Set steps per mm
M566 X900.00 Y900.00 Z900.00 E120.00         ; Set maximum instantaneous speed changes (mm/min)
M203 X18000.00 Y18000.00 Z3000.00 E1200.00     ; Set maximum speeds (mm/min)
M201 X500.00 Y500.00 Z500.00 E250.00         ; Set accelerations (mm/s^2)
M906 X1100.00 Y1100.00 Z1000.00 E1000.00 I25 ; Set motor currents (mA) and motor idle factor in per cent
M84 S30                                      ; Set idle timeout

; Axis Limits
M208 X-3 Y0 Z0 S1                            ; Set axis minima
M208 X400 Y620 Z10000000000000000 S0         ; Set axis maxima

; Endstops
M574 X1 Y1 S1                                ; Set active high endstops

; Z-Probe
M558 P1 H5 F120 T6000                        ; Set Z probe type to unmodulated and the dive height + speeds
G31 P500 X0 Y0 Z2.5                          ; Set Z probe trigger value, offset and trigger height
M557 X15:15 Y15:195 S20                      ; Define mesh grid

; Heaters
M305 P0 T100000 B4267 R4700                  ; Set thermistor + ADC parameters for heater 0
M143 H0 S110                                 ; Set temperature limit for heater 0 to 110C
M305 P1 T500000 B4723 C1.196220e-7 R4700     ; Set thermistor + ADC parameters for heater 1 Slice Hightemp
M143 H1 S450                                 ; Set temperature limit for heater 1 to 450C

; Fans
M106 P0 S0.3 I0 F500 H-1                     ; Set fan 0 value, PWM signal inversion and frequency. Thermostatic control is turned off
M106 P1 S1 I0 F500 H1 T45                    ; Set fan 1 value, PWM signal inversion and frequency. Thermostatic control is turned on

; Tools
M563 P0 S"Mosquito" D0 H1                    ; Define tool 0
M572 D0 S0.2                                 ; enable pressure advance
G10 P0 X0 Y0 Z0                              ; Set tool 0 axis offsets
G10 P0 R0 S0                                 ; Set initial tool 0 active and standby temperatures to 0C

; Automatic saving after power loss is not enabled

; Custom settings are not configured

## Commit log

2019-02-19 Folder Restructute
    folder restructure
    [1-All_Belt_Clamps V2.stl, 1-Belt stepper mount Pt1 V4.stl, 1-CBA bottom Cover V3 - part 1of3.stl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]
2019-02-20 configuration files
    [bed.g, cancel.g, config-override.g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]
2019-02-20 renamed folder
    [4080 to 2040 drill alignment tool.stl, linear rail alignment tool 2.stl, linear_rail_alignment_tool.stl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]
2019-03-27 Added BOM
    [White Knight Documentation.xlsx]
2019-03-29 update 28 March 2019
    [White Knight Documentation.xlsx]
2019-04-03 added markdown tables
    converted the original xlsx spreadsheet and order pdf's into a single readme.md with markdown tables
    [White Knight Documentation.xlsx]
2019-04-03 Updated Stepper mount files
    Added a hole in each stepper mount for a physical end stop screw..
2019-04-04 added pdf's and xlsx back
    [White Knight Documentation.xlsx]
2019-04-06 White Knight Panel Due 7i enclosure
    I've added the embossed enclosure for the Panel Due 7i
    [1-PanelDue_7i_Version_2_Back.stl, 1-PanelDue_7i_Version_2_Front WK.stl]
2019-04-09 Added Wire Harness to BOM
2019-04-11 Update White Knight Documentation.xlsx
    [White Knight Documentation.xlsx]
2019-04-12 Added Trip tray & handle
    Added the Drip tray and drip tray handle files
    [Drip Tray handle.stl]
2019-04-12 Update Readme
    Added basic print setting for each file..
2019-04-12 Update readme.md
    Added power switch to BOM
2019-04-14 Update readme.md
    updated source and part # for Meanwell power supply.. saved $12 from BOM This tip came from AzonicTech… Thanks
2019-04-15 updated plate designs
    offset the plate to align with belt position and added rounded edges for leading edge of hot plate and exit edge of cold plate..
    [1x-Cold Build Plate V3.stl, 1x-Heated Build Plate V3.stl]
2019-04-15 Update readme.md
    added fittings and PTFE tube for wire run to hotend
2019-09-14 Loaded Fusion files
    Loaded Fusion 360 files to Master Directory
    [1-Belt stepper mount Pt1 V4 v3.f3d, 1-Belt_Clamp_2 v3.f3d, 1-Belt_Clamp_3 v4.f3d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]
2019-09-14 Added STEP files
    Added STEP files to Fusion 360 folder
    [1-Belt stepper mount Pt1 V4 v3.step, 1-Belt_Clamp_2 v3.step, 1-Belt_Clamp_3 v4.step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]
2019-10-18 Added Squire Fusion 360 files
    Uploaded fusion 360 files for the Squire.
    [1-5i_Case_Front v4.f3d, 1-5i_Case_Rear v7.f3d, 1-Belt Stepper direct drive Mount2 v2.f3d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]
2019-10-20 added Step files to Squire folder
    [1-5i_Case_Front v4.step, 1-5i_Case_Rear v7.step, 1-Belt Stepper direct drive Mount2 v2.step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]
2019-10-20 Added STL files.
    [1-5i_Case_Front Knight v14.stl, 1-5i_Case_Front v4.stl, 1-5i_Case_Rear v7.stl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]
2019-10-20 Added Assembly files
2019-10-20 Create White Knight Full Assembly v123.f3z
2019-10-22 Updated STL file orientation
    Set all STL's to proper print orientation
    [1-5i_Case_Front Knight v14.stl, 1-5i_Case_Front v4.stl, 1-5i_Case_Rear v7.stl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]
2019-10-26 Added BOM
    Some of the hardware counts may not be accurate but are within minum McMaster order quantities..
2019-10-29 Updated Assembly file
    made changes to heated build plate size
2019-10-30 updated BOM's
    updated BOM's
2019-10-30 Updated BOM's
2019-11-17 Uploaded V125 of assembly
    added F623ZZ bearing for GT2 belt runs
2019-12-16 updated Belt stepper mount
    Updated Belt stepper mount with V3 version.. Peeler will need to be updated to clear new design..
    [1-Belt Stepper direct drive Mount2 v2.f3d, 1-Belt Stepper direct drive Mount2 v2.step, 1-Belt Stepper direct drive Mount2 v2.stl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]
2020-01-20 Updated master assembly
    updated assembly with new direct drive roller stepper mount and new version of peeler..
2020-01-20 Updated Peeler file
    Updated Peeler files to version 4
    [1-Peeler V4 v2.f3d, 1-Peeler V4 v2.step, 1-Peeler V4 v2.stl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]
2020-01-20 Update readme.md
    added buck converter that was missing from BOM.
2020-03-29 Added belt steppr mount for E3D
    added files for a Belt stepper mount designed to work with the E3D 5:1 stepper..
    [1-Belt Stepper direct drive Mount2 for E3D v2.f3d, 1-Belt Stepper direct drive Mount2 for E3D v2.step, 1-Belt Stepper direct drive Mount2 for E3D v2.stl]
2020-04-15 Update readme.md
    Corrected build plate size
2020-04-18 Update readme.md
    updated fan quantity.
2020-04-27 Updated assembly file
    Updated assembly file and included Step and IGES file types
2020-06-17 Update readme.md
    new item specs for roller axle shaft
2020-06-17 Update readme.md
    updated roller axle shaft specs
2020-07-19 Added 4 part CBA slide tray
    Added a 4 part version of the CBA slide tray.
    [CBA _Slide_Tray_Part_1of4 v2.f3d, CBA _Slide_Tray_Part_1of4 v2.step, CBA _Slide_Tray_Part_1of4 v2.stl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]
2020-09-28 Added WhiteKnight belt stepper mount modified to fit bolt pattern of geared stepper LDO-42STH40-1204ACPG5 sold by Printed Solid
    [1-Belt stepper mount Pt1 - LDO-42STH40-1204ACPG5 - V1.f3d, 1-Belt stepper mount Pt1 - LDO-42STH40-1204ACPG5 - V1.step, 1-Belt stepper mount Pt1 - LDO-42STH40-1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]
2020-11-18 added M3x40mm screws to hardware list
2020-11-18 fixing issue #63
    Attempting to correcting download issue #63
    [2-Roller_Insert.stl]
2020-11-18 Update 2-Side_Support_Bottom_Brace.stl
    #63 attempt 3 to fix
2021-02-27 Added buck converter.
